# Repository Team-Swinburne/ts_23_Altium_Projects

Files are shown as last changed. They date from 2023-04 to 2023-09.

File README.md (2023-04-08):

# About

A Github repository by Team Swinburne for pcb development of the TS_22 vehicle and experimental projects. This will only contain files of the actual pcb design, more information such as design choice, circuit theory, simulation, etc can be located in the shared Pne Drive

# Getting Started

### Prerequisites
- [Altium](https://www.altium.com/solutions/academic-programs/student-licenses) (required): Used to design all of these pcb, fill in the link for a free student license.
- [Git](https://git-scm.com/) (required) : Backbone of Github.
- [Github Destop](https://desktop.github.com/) (recommended) : An UI overlay of git built specifically for Github so you don't have to deal with the terminal interface.

### Installation
Once all prerequisite are install, clone this repository to your desired folder by opening it in Github Desktop


# Usage
Follow this guide to ensure you meet the standard and is set up probably before diving into create your own pcb

### Naming
**Always** name your project strictly following the naming scheme to avoid confusion in the future. When starting a new board, create a new folder name `ts_22-"Board name"`. Then inside that folder, create a project in Altium called `YYMMDD "Board name" "Revsion number"`
#### For example:
> ts_22-Brake-Module
>
Then:
> 210705 Brake Module R0
> 
`YYMMDD` is the project's createtion date and `Revision number` starts with 0. 
#### Note: Once the pcb is made, **DO NOT** make any changes to that revision, modifying **MUST** be made by starting a new revision, e.g. R1

### Importing libraries
Altium libraries are collections of component intented for speeding up the design and manufacturing process. There are 2 libraries used in PnE: *ts_22-standard-lib* and *ts_22-connectors-lib*, located in the *~ts_22 Library*.

To import them: In Altium with your project opened, right-click on the project name -> Add Existing -> Choose file `"library name".DbLib`, do this for both libraries.



Guide on how to add components into the library will be made available in video from. Please discuss with your section leader before attempting to modify these library.

### Importing design rules
Design rules ensure all pcb meet Team Swinburne standards and more importantly, the competition rule. There are 2 sets of rules: *ts_22-rules.RUL* and *ts_22-HV-rules.RUL*. Choose the corresponding rule dependent on which board you are working on.

To import: In Altium with your project opened, choose Design -> Rules. Then in the pop-up windows, right-click on Design Rules -> Import Rules -> Select all entries -> OK -> Choose file `"rules name".RUL`.



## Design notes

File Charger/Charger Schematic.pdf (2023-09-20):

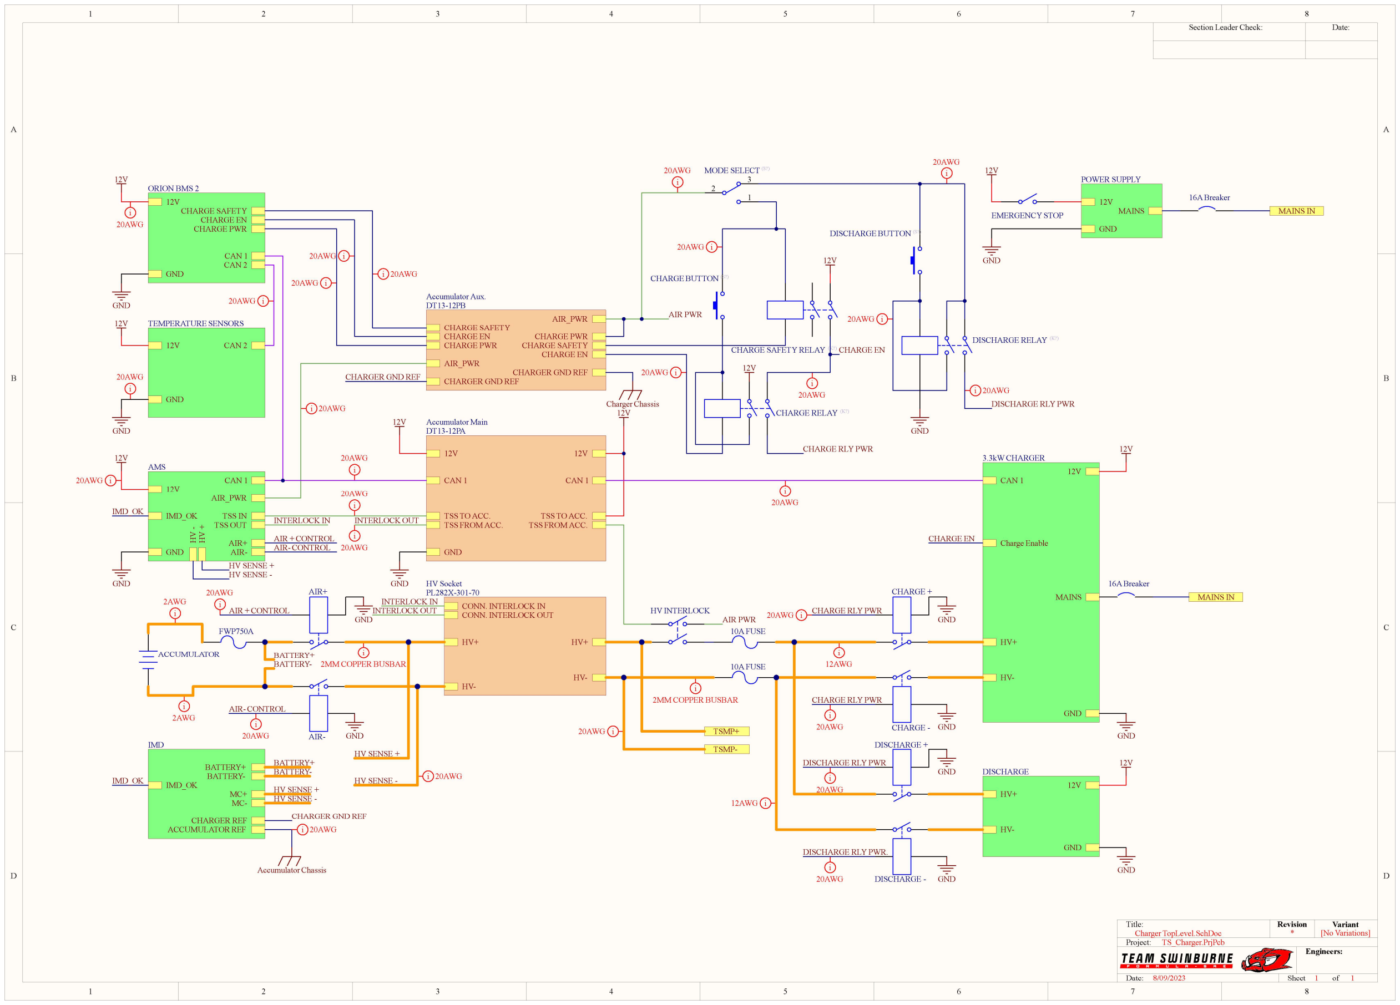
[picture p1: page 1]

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
Engineers:

Date: | Sheet | of 8/09/2023 | 1 | 1

Project:

Title: | Revision | Variant
Section Leader Check: | Date:

Charger TopLevel.SchDoc
TS_Charger.PrjPcb

* [No Variations]

12V

GND

CHARGE PWR

CHARGE SAFETY
CHARGE EN

CAN 1
CAN 2

ORION BMS 2

12V

GND

CAN 2

GND

12V

12V TEMPERATURE SENSORS

GND

CAN 1

GND

12V HV ⁻ HV ⁺

TSS IN
TSS OUT

AIR_PWR

AIR+
AIR-

IMD_OK

AMS

GND

12V

CHARGE SAFETY
CHARGE EN
CHARGE PWR

AIR_PWR

AIR_PWR

CHARGE SAFETY
CHARGE EN

CHARGE PWR

CHARGER GND REF

CHARGER GND REF

Accumulator Aux.
DT13-12PB

12V

GND

CAN 1

TSS TO ACC.
TSS FROM ACC.

TSS TO ACC.
TSS FROM ACC.

12V

CAN 1

Accumulator Main
DT13-12PA

12V

GND

HV+

HV-

HV+

HV-

CONN. INTERLOCK IN
CONN. INTERLOCK OUT

HV Socket
PL282X-301-70

12V

GND

MAINS

POWER SUPPLY

12V

GND

DISCHARGE RELAY (K?)

16A Breaker
MAINS IN

DISCHARGE BUTTON ⁽S?)

2

3

1

MODE SELECT ⁽S?)

12V

CHARGE SAFETY RELAY (K?)

12V

GND

DISCHARGE RLY PWR

CHARGE EN

CHARGE RELAY (K?)

CHARGE BUTTON ⁽S?)

12V

CHARGE RLY PWR

HV INTERLOCK

AIR PWR

AIR PWR

CAN 1

GND

12V

HV+

HV-

MAINS

Charge Enable

3.3kW CHARGER

CHARGE -

CHARGE +

GND

GND

CHARGE RLY PWR

CHARGE RLY PWR

GND

12V

16A Breaker
MAINS IN

10A FUSE

10A FUSE

DISCHARGE -

DISCHARGE +

GND

GND

DISCHARGE RLY PWR

DISCHARGE RLY PWR.

CHARGE EN

HV+

GND

12V

HV-

DISCHARGE

GND

12V

TSMP+

TSMP-

AIR-

AIR+

GND

GND

AIR + CONTROL

AIR- CONTROL

AIR + CONTROL
AIR- CONTROL

ACCUMULATOR

FWP750A

HV SENSE +
HV SENSE -

HV SENSE +

HV SENSE - | i 20AWG

i

20AWG

i

20AWG

i
20AWG

20AWG i

i

20AWG

20AWG i

i
20AWG

i 20AWG
20AWG i

20AWG i

i 20AWG

i

20AWG

i
20AWG

20AWG i

i
20AWG

i
20AWG

i
20AWG

i
20AWG

20AWG i

20AWG i

i

20AWG | i 20AWG

i 20AWG

20AWG i

i
20AWG

i
12AWG

12AWG i

i
2MM COPPER BUSBAR

20AWG i

i

2AWG

i
2AWG

i
2MM COPPER BUSBAR

BATTERY+
BATTERY-IMD_OK

CHARGER REF
ACCUMULATOR REF

MC+
MC-

IMD

EMERGENCY STOP

INTERLOCK IN

INTERLOCK IN
INTERLOCK OUT

INTERLOCK OUT

HV SENSE +
HV SENSE -

BATTERY+
BATTERY-

BATTERY+
BATTERY-

Accumulator Chassis

IMD_OK

IMD_OK

Charger Chassis

CHARGER GND REF

CHARGER GND REF
i 20AWG

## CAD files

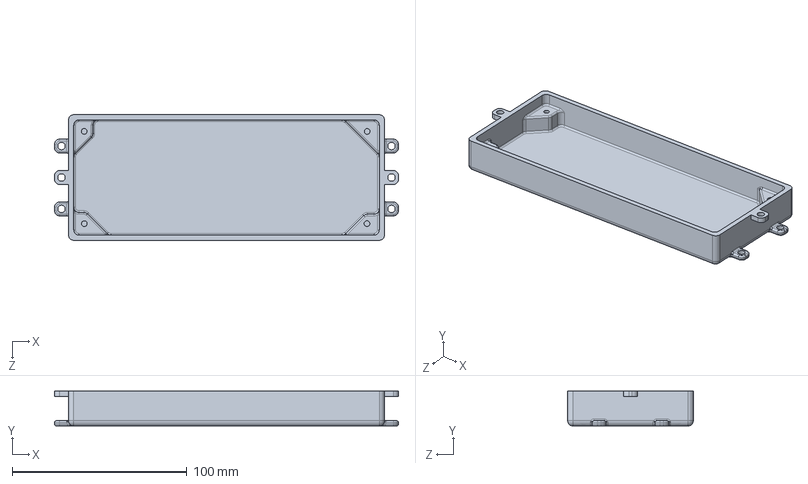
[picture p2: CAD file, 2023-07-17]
TS_23_Temp Expansion Module/Temp Module Assembly CAD/Temp_Module_Enclosure_Base.SLDPRT
197.0 x 20.0 x 72.0 mm

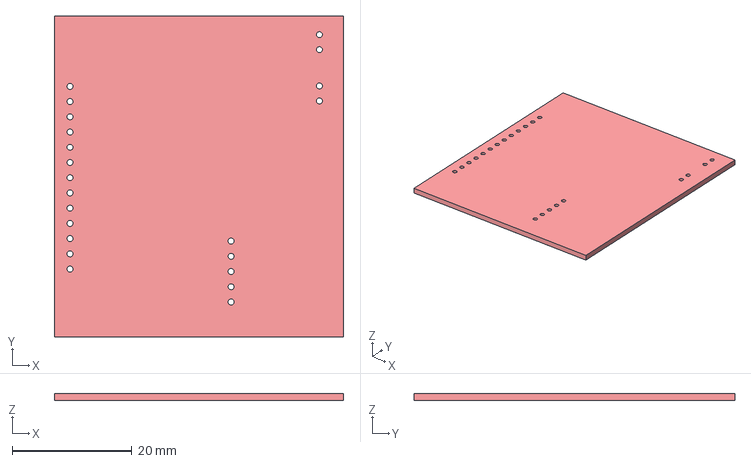
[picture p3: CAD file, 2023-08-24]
ts_23_BMS_SLAVE/LVBMS_A_Sample_R2/LVBMS_A_Sample_R2.step
48.2 x 53.5 x 1.20 mm

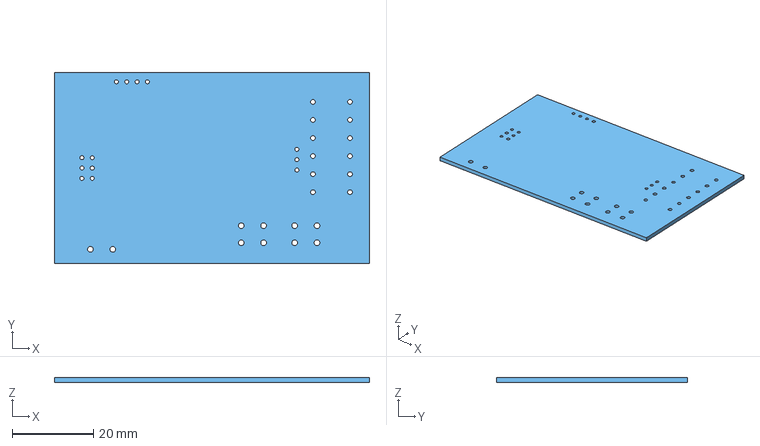
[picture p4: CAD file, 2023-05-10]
ts_23_LV_BMS_MASTER/LV_MASTER_A_SAMPLE/LV_MASTER_A_SAMPLE.step
77.5 x 46.9 x 1.20 mm

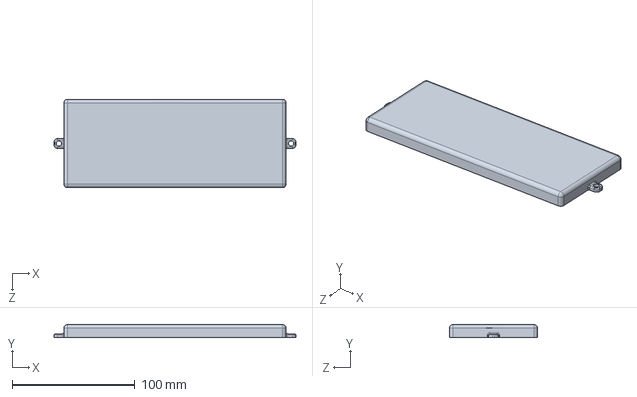
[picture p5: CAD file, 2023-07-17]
TS_23_Temp Expansion Module/Temp Module Assembly CAD/Temp_Module_Enclosure_Lid.SLDPRT
197.0 x 10.5 x 72.0 mm

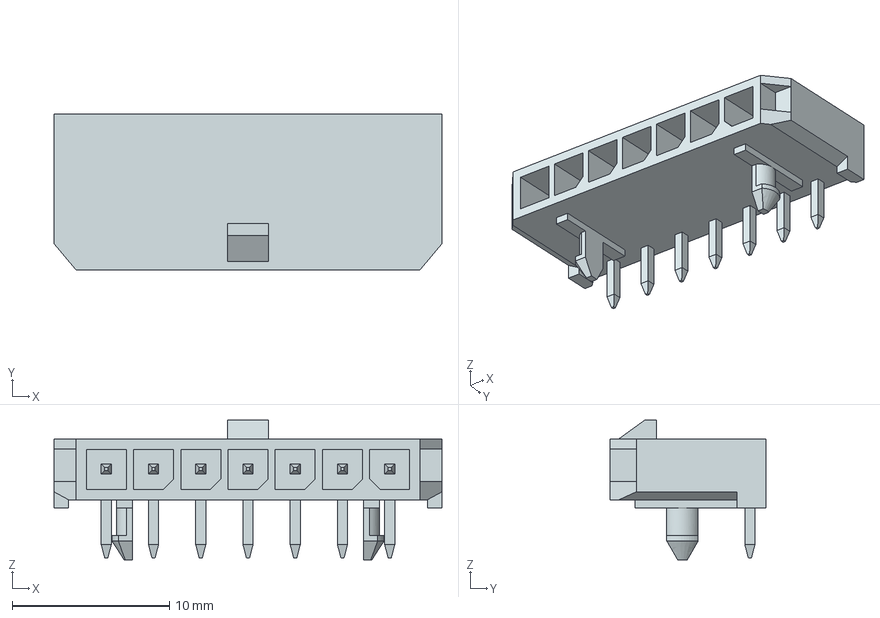
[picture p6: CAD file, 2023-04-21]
TS_23 Dashboard Breakout Board/436500700.stp
24.6 x 9.90 x 8.87 mm

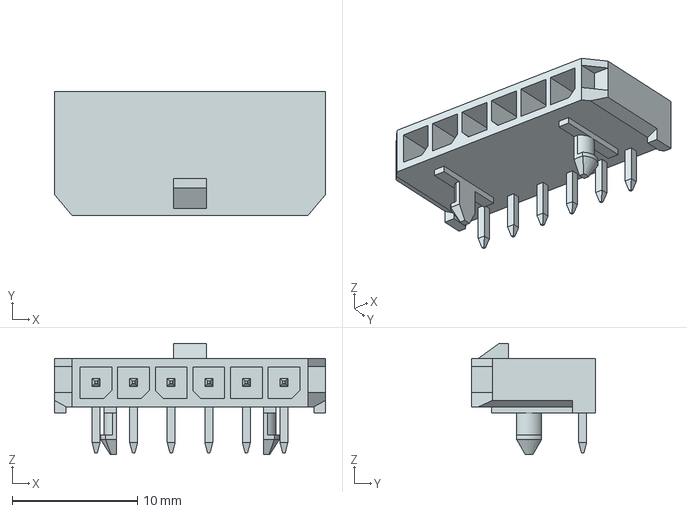
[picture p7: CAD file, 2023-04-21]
TS_23 Dashboard Breakout Board/436500600.stp
21.6 x 9.90 x 8.87 mm

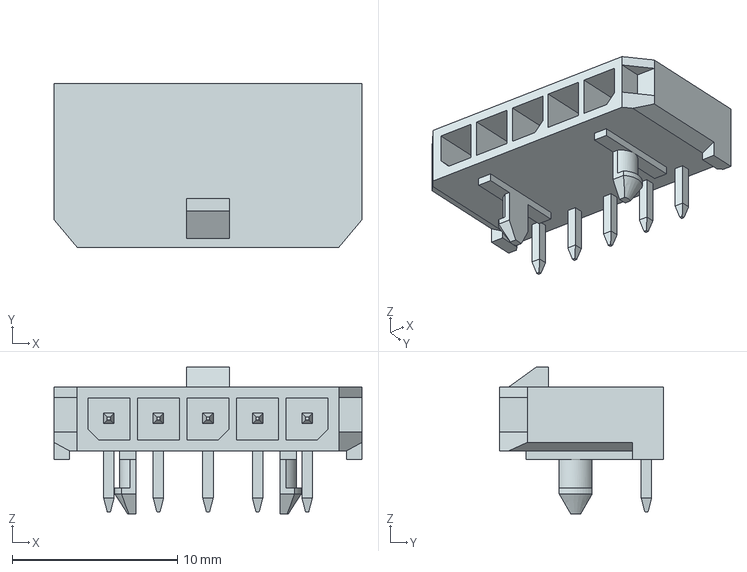
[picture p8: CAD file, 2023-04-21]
TS_23 Dashboard Breakout Board/436500500.stp
18.6 x 9.90 x 8.87 mm

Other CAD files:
ts_23_BMS_SLAVE/LVBMS_A_Sample_R2/LVBMS_A_Sample_R2 PCB.step.SLDPRT
ts_23_LV_BMS_MASTER/LV_MASTER_A_SAMPLE/LV_MASTER_A_SAMPLE PCB.step.SLDPRT

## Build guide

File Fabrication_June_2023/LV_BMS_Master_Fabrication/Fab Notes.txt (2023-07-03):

------------------------------------
-----LV BMS MASTER FAB NOTES-------
-----------------------------------

Qty: 5
Dimensions: 90.5mm X 49.9mm
Layers: 4
Signal Layers: 1, 2
	a) Weight: 1oz
Solder Mask: Blue
Silkscreen: White
Surface Finish: ENIG
Finished Copper: 2oz Cu
Total Thickness: 1.6mm

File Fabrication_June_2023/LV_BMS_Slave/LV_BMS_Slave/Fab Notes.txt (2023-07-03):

------------------------------------
-----LV BMS Slave Fab Notes-------
-----------------------------------

Qty: 10
Dimensions: 48.2mm X 53.5mm
Layers: 2
Signal Layers: 1, 2
	a) Weight: 1oz
Solder Mask: Red
Silkscreen: White
Surface Finish: ENIG
Finished Copper: 2oz Cu
Total Thickness: 1.6mm

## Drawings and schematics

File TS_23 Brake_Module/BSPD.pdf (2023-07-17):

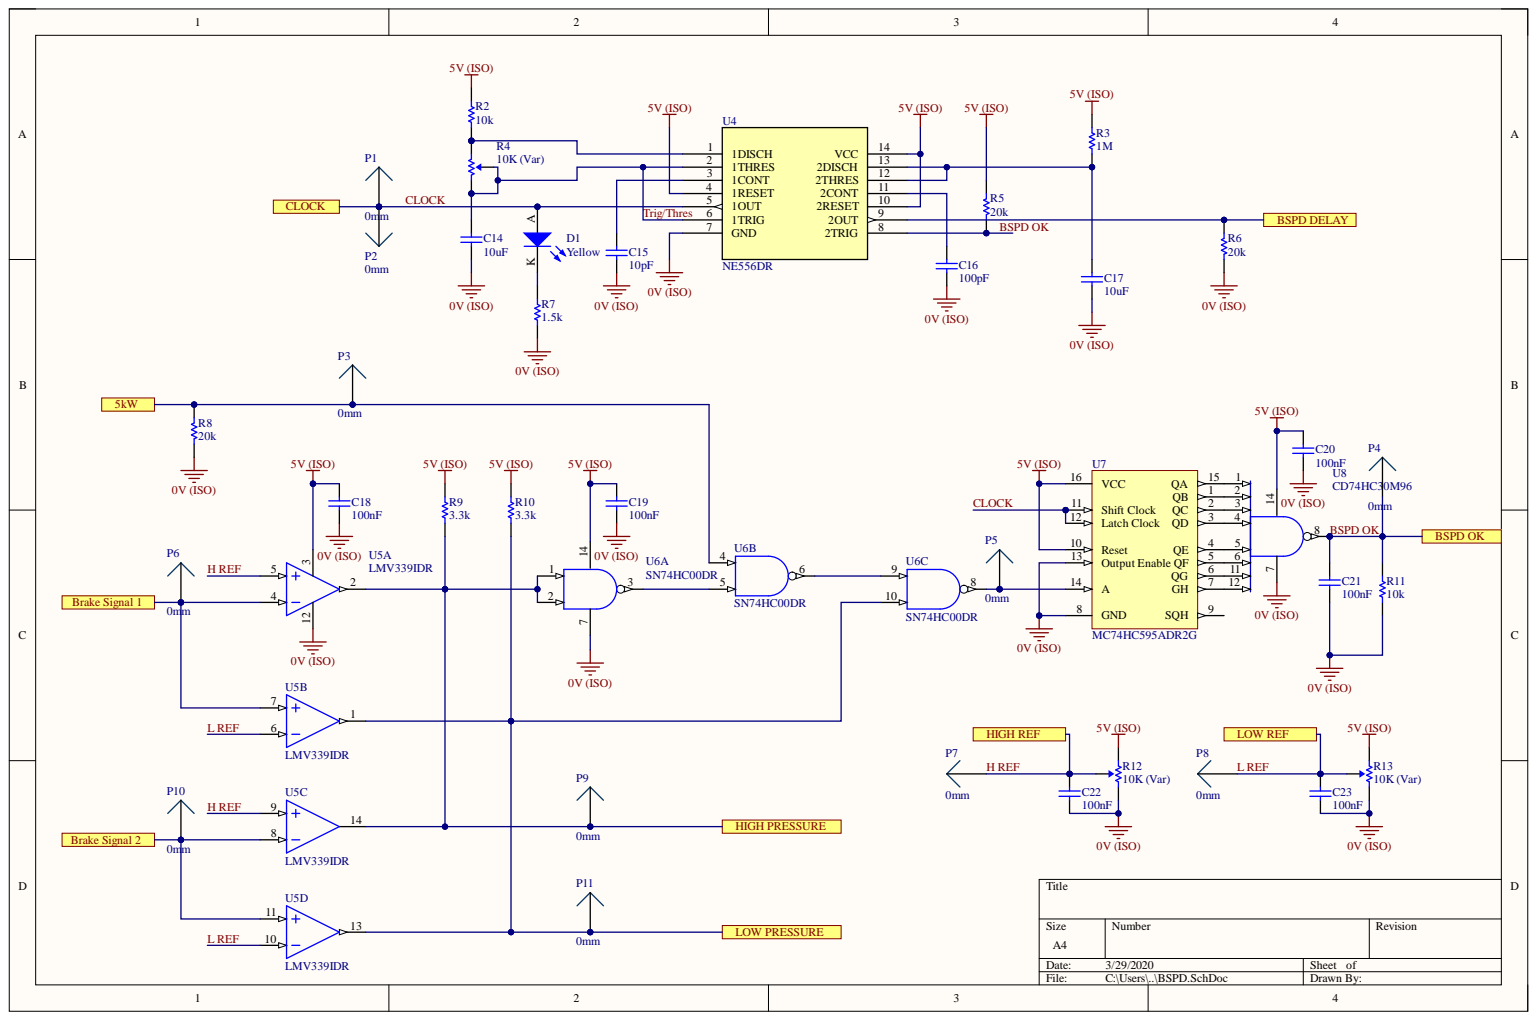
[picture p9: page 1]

1THRES 2

1RESET 4

Trig/Thres | 1TRIG 6

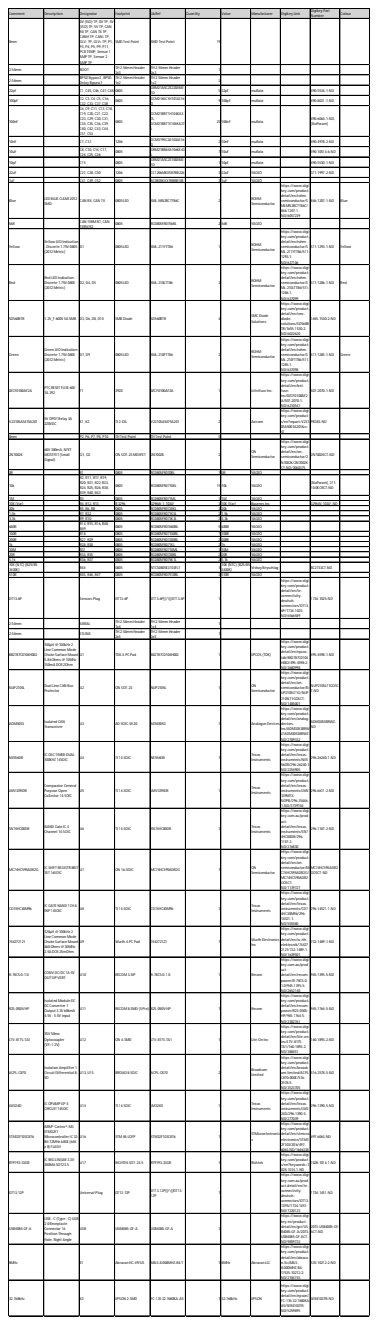
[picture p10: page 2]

Comment | Description | Designator | Footprint | LibRef | Quantity | Value | Manufacturer | Digikey Link | Digikey Part Number | Colour

0mm | | 0V (ISO) TP, 0V TP, 5V (ISO) TP, 5V TP, CAN RX TP, CAN TX TP, CANH TP, CANL TP, GLV- TP, GLV+ TP, P1, P3, P4, P5, P9, P11, PCB TEMP, Sensor 1 AMP TP, Sensor 2 AMP TP | SMD Test Point | SMD Test Point | 19

2.54mm | | BOOT | TH 2.54mm Header 2x3 | TH 2.54mm Header 2x3 | | 1

2.54mm | | BPSD Bypass1, BPSD Delay Bypass1 | TH 2.54mm Header 1x2 | TH 2.54mm Header 1x2 | | 2

22pF | | C1, C45, C46, C47, C48 | 0805 | GRM21A5C2E220JW0 1D | | 5 22pF | muRata | | 490-5534-1-ND

100pF | | C2, C3, C4, C5, C16, C32, C33, C37, C38 | 0805 | GCM2165C1H101JA16 D | | 9 100pF | muRata | | 490-8031-1-ND

100nF | | C6, C9, C11, C13, C18, C19, C20, C21, C22, C23, C29, C30, C31, C34, C35, C36, C39, C40, C42, C43, C44, C51, C53 | 0805 | GCM21BR71H104KA3 7L, GCM21BR71E104KA37 L | 23 100nF | | muRata | | 490-6064-1-ND, [NoParam]

10nF | | C7, C12 | 1206 | GCM3195C2A103JA16 D | | 2 10nF | muRata | | 490-4978-2-ND

10uF | | C8, C10, C14, C17, C24, C25, C26 | 0805 | GRM21BR6YA106KE43 L | | 7 10uF | muRata | | 490-10514-6-ND

10pF | | C15 | 0805 | GRM21A5C2E100JW0 1D | | 1 10pF | muRata | | 490-5530-1-ND

22uF | | C27, C28, C50 | 1206 | CC1206MKX5R7BB226 | | 3 22uF | YAGEO | | 311-1997-2-ND

1uF Blue | LED BLUE CLEAR 2012 SMD | C41, C49, C52 CAN RX, CAN TX | 0805 0805 LED | AC0805KKX7R8BB105 SML-MN2BCTT86C | | 3 1uF 2 | YAGEO ROHM Semiconductor | https://www.digikey.com/product-detail/en/rohm-semiconductor/SMLMN2BCTT86C/846-1207-1-ND/6057239 | 846-1207-1-ND | Blue

56R | | CAN TERM R1, CAN TERM R2 | 0805 | RC0805FR0756RL | 2 56R | YAGEO

Yellow | Yellow LED Indication - Discrete 1.75V 0805 (2012 Metric) | D1 | 0805 LED | SML-211YTT86 | 1 | ROHM Semiconductor | https://www.digikey.com/product-detail/en/rohm-semiconductor/SML-211YTT86/511-1293-1-ND/637106 | 511-1293-1-ND | Yellow

Red | Red LED Indication -Discrete 1.75V 0805 (2012 Metric) | D2, D4, D5 | 0805 LED | SML-210LTT86 | 3 | ROHM Semiconductor | https://www.digikey.com/product-detail/en/rohm-semiconductor/SML-210LTT86/511-1286-1-ND/637099 | 511-1286-1-ND | Red

SD560BTR | 1.2V_F 600V 5A SMB | D3, D6, D8, D10 | SMB Diode | SD560BTR | 4 | SMC Diode Solutions | https://www.digikey.com/product-detail/en/smc-diode-solutions/SD560BTR/1655-1530-2-ND/6022620 | 1655-1530-2-ND

Green | Green LED Indication -Discrete 1.75V 0805 (2012 Metric) | D7, D9 | 0805 LED | SML-210FTT86 | 2 | ROHM Semiconductor | https://www.digikey.com/product-detail/en/rohm-semiconductor/SML-210FTT86/511-1285-1-ND/637098 | 511-1285-1-ND | Green

0ZCF0100AF2A | PTC RESET FUSE 60V 1A 292 | F1 | 2920 | 0ZCF0100AF2A | 1 | Littelfuse Inc. | https://www.digikey.com/product-detail/en/bel-fuse-inc/0ZCF0100AF2A/507-2070-1-ND/6210547 | 507-2070-1-ND

V23105A5475A201 | 5V DPDT Relay 3A 220VDC | K1, K2 | TI 2-DIL | V23105A5475A201 | 2 | Axicom | https://www.digikey.com/products/en?mpart=V23105A5001A201&v=41 | PB383-ND

0mm 2N7002K | 60V 380mA, NFET MOSTFET (Small Signal) | P2, P6, P7, P8, P10 Q1, Q2 | TH Test Point ON SOT-23 MOSFET | TH Test Point 2N7002K | 5 2 | ON Semiconductor | https://www.digikey.com/product-detail/en/on-semiconductor/2N7002K/2N7002KCT-ND/2060375 | 2N7002KCT-ND

0R 10k | R1 R2, R11, R17, R19, R20, R21, R22, R23, R24, R25, R26, R38, R39, R40, R43 | 0805 | RC0805FR070RL RC0805FR0710KL | 15 10k | 1 0R | YAGEO | [NoParam], 311-10.0KCRCT-ND

5.1k 10K (NTC) (B25/85 3430K) | R36, R37 R44 | 0805 | RC0805FR075K1L NTCS0805E3103FLT | 2 5.1k 1 10K (NTC) (B25/85 3430K) | YAGEO Vishay Beyschlag | BC2733CT-ND

510R DT13-6P | R45, R46, R47 Sensors Plug | 0805 DT13-6P | RC0805FR07510RL DT13-6P[[/\]]DT13-6P | 3 510R 1 | YAGEO | https://www.digikey.com/product-detail/en/te-connectivity-deutsch-connectors/DT13-6P/1734-1025-ND/6566589 | 1734-1025-ND

2.54mm | | SERIAL | TH 2.54mm Header 1x4 | TH 2.54mm Header 1x4 | 1

2.54mm | | STLINK | TH 2.54mm Header 2x5 | TH 2.54mm Header 2x5 | 1

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

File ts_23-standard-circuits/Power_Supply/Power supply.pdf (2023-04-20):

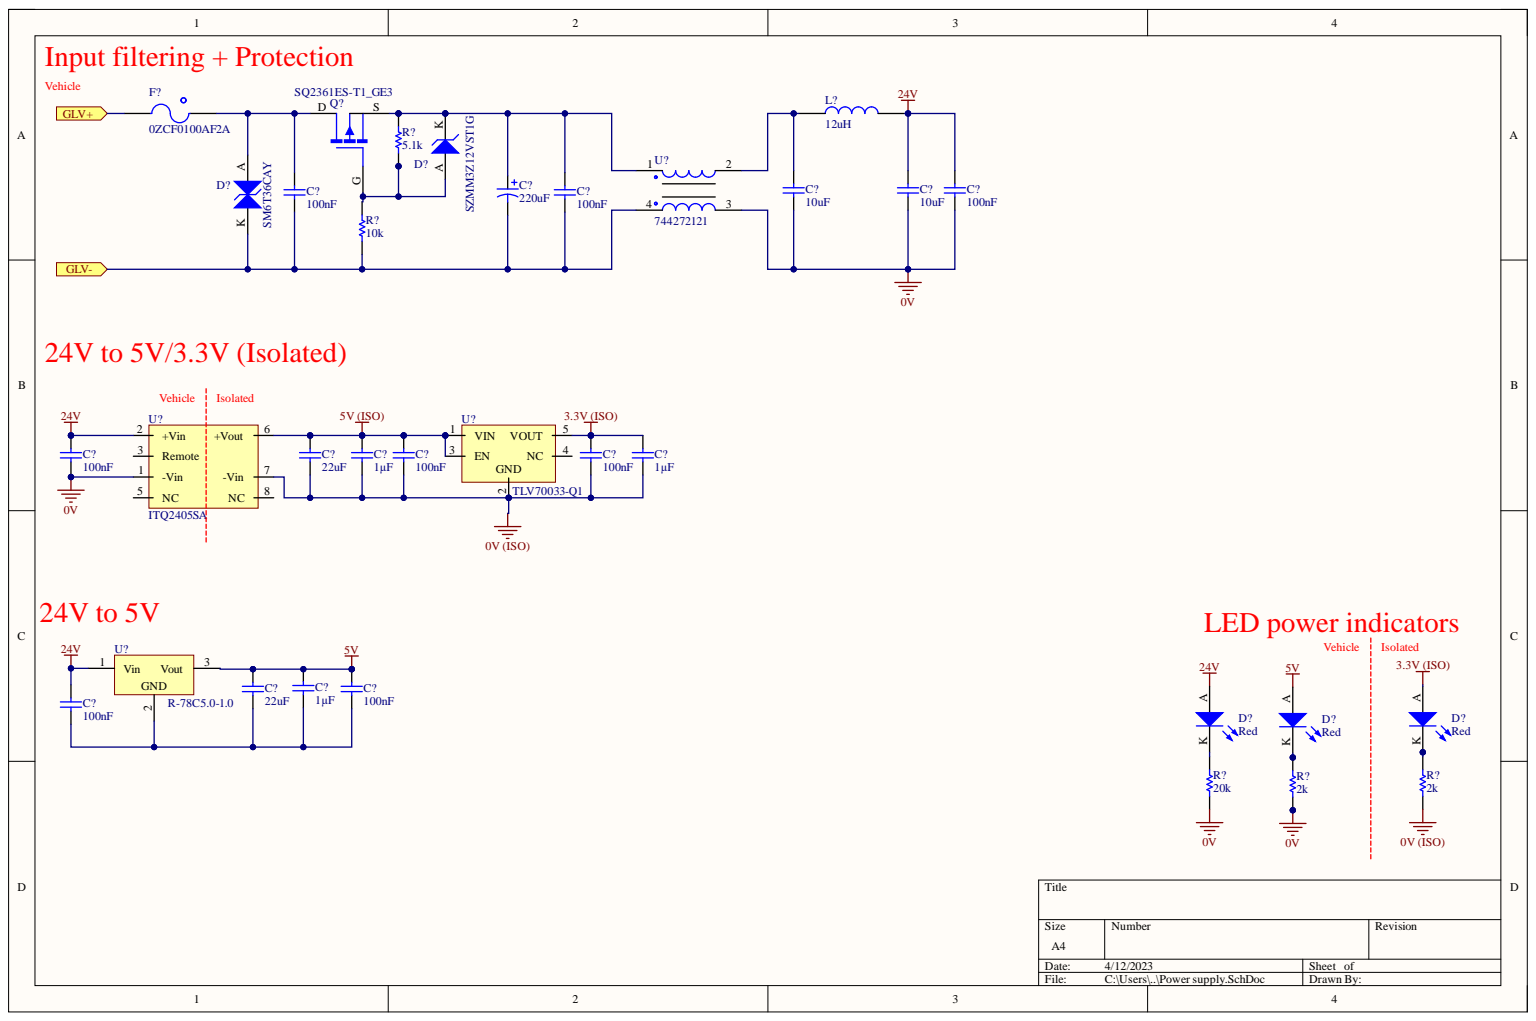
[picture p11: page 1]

Comment | Description | Designator | Footprint | LibRef | Quantity
220uF | | C6, C? | Vishay Radial 1213 | MAL214699106E3 | 2
10uF | | C7, C8, C? | 0805 | GRM21BR6YA106KE4 3L | 4
100nF | | C9, C10, C11, C12, C15, C16, C? | 0805 | GCM21BR71H104KA3 7L | 12
22uF | | C13, C? | 0805 | GRM21BR61A226ME5 1L | 2
1µF | | C14, C17, C? | 0805 | GCM21BR71H105KA0 3L | 4
SZMM3Z12VST1G | | D2, D? | ON SOD323 | SZMM3Z12VST1G | 2
SM6T36CAY | | D3, D? | ST SMB DIODE | SM6T36CAY | 2
Red | [NoValue], Red LED Indication - Discrete 1.75V 0805 (2012 Metric) | D4, D5, D? | 0805 LED | Red, SML-210LTT86 | 4
0ZCF0100AF2A | PTC RESET FUSE 60V 1A 292 | F2, F? | 2920 | 0ZCF0100AF2A | 2
12uH | | L1, L? | 1812 | RLS-126 | 2
SQ2361ES-T1_GE3 | MOSFET P-CH 60V 2.8A SSOT23 | Q1, Q? | VSHY SOT-23-3 | SQ2361ES-T1_GE3 | 2
5.1k | | R1, R? | 0805 | RC0805FR075K1L | 2
10k | | R2, R? | 0805 | RC0805FR0710KL | 2
20k | | R3, R? | 0805 | RC0805FR0720KL | 2
2k | | R4, R? | 0805 | RC0805FR072KL | 2
744272121 | | U3, U? | Wurth 4-PC Pad | 744272121 | 2
ITQ2405SA | DC DC CONVERTER 5V 6W | U4, U? | 8-SIP | ITQ2405SA | 2
TLV70033-Q1 | IC REG LINEAR 3.3V 200MA SOT23-5 | U5, U? | TI SOT-23-5 | TLV70033-Q1 | 2

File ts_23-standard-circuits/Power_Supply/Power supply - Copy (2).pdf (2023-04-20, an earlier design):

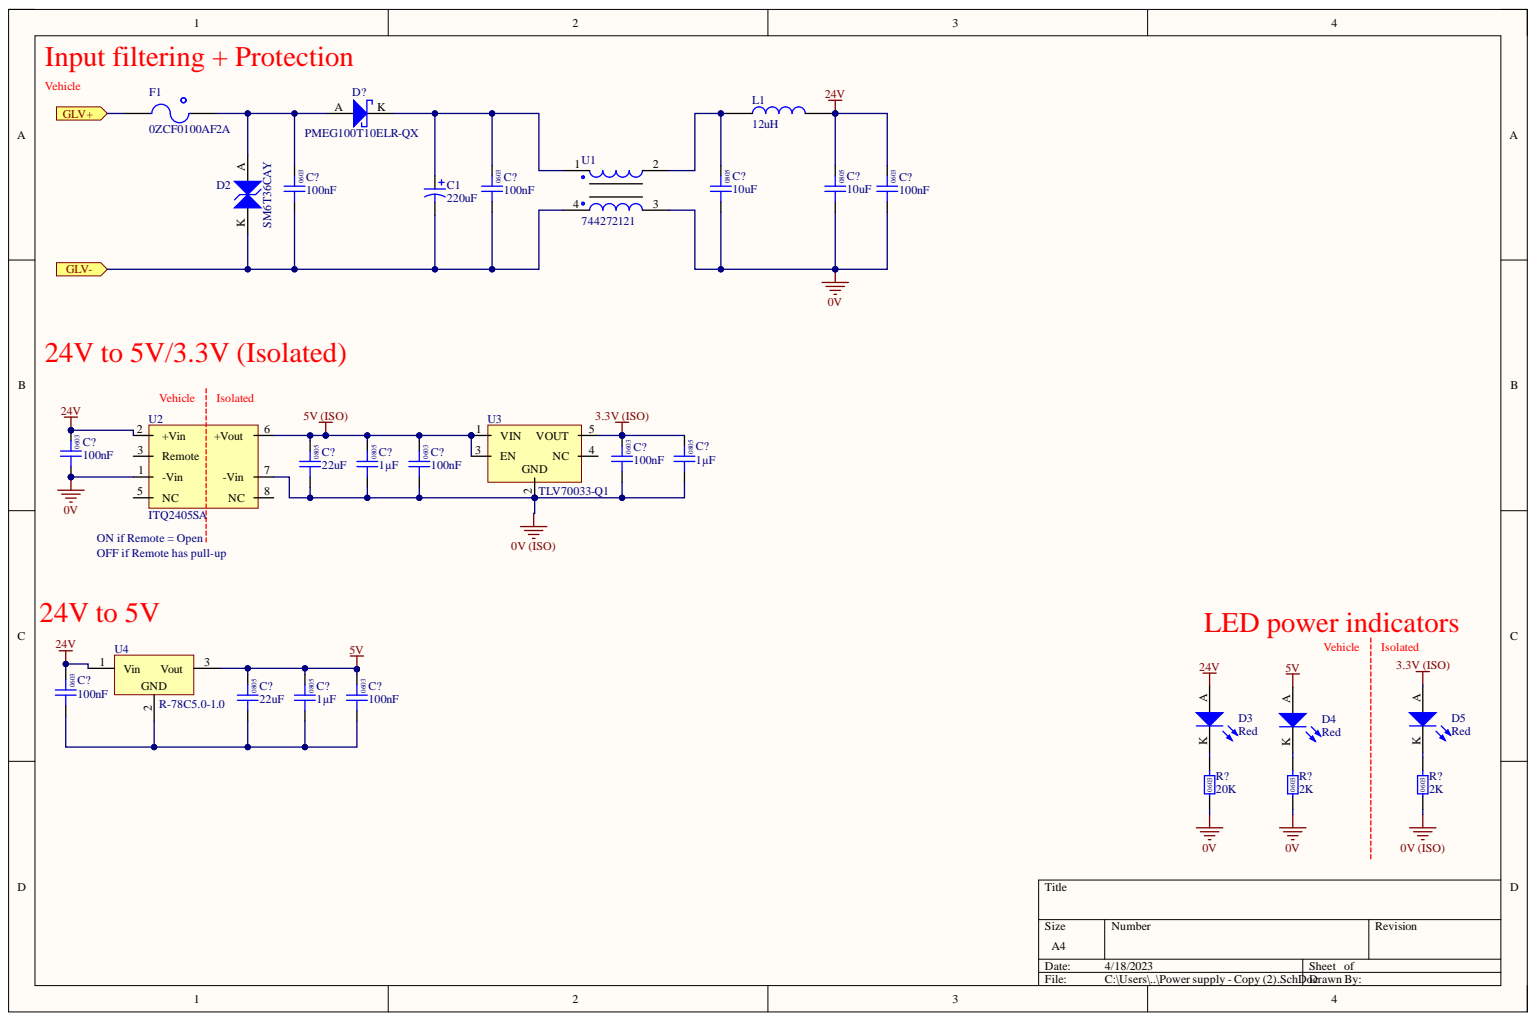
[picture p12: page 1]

Remote 3 -Vin 1 | EN 3

TLV70033-Q1

ON if Remote = Open
OFF if Remote has pull-up

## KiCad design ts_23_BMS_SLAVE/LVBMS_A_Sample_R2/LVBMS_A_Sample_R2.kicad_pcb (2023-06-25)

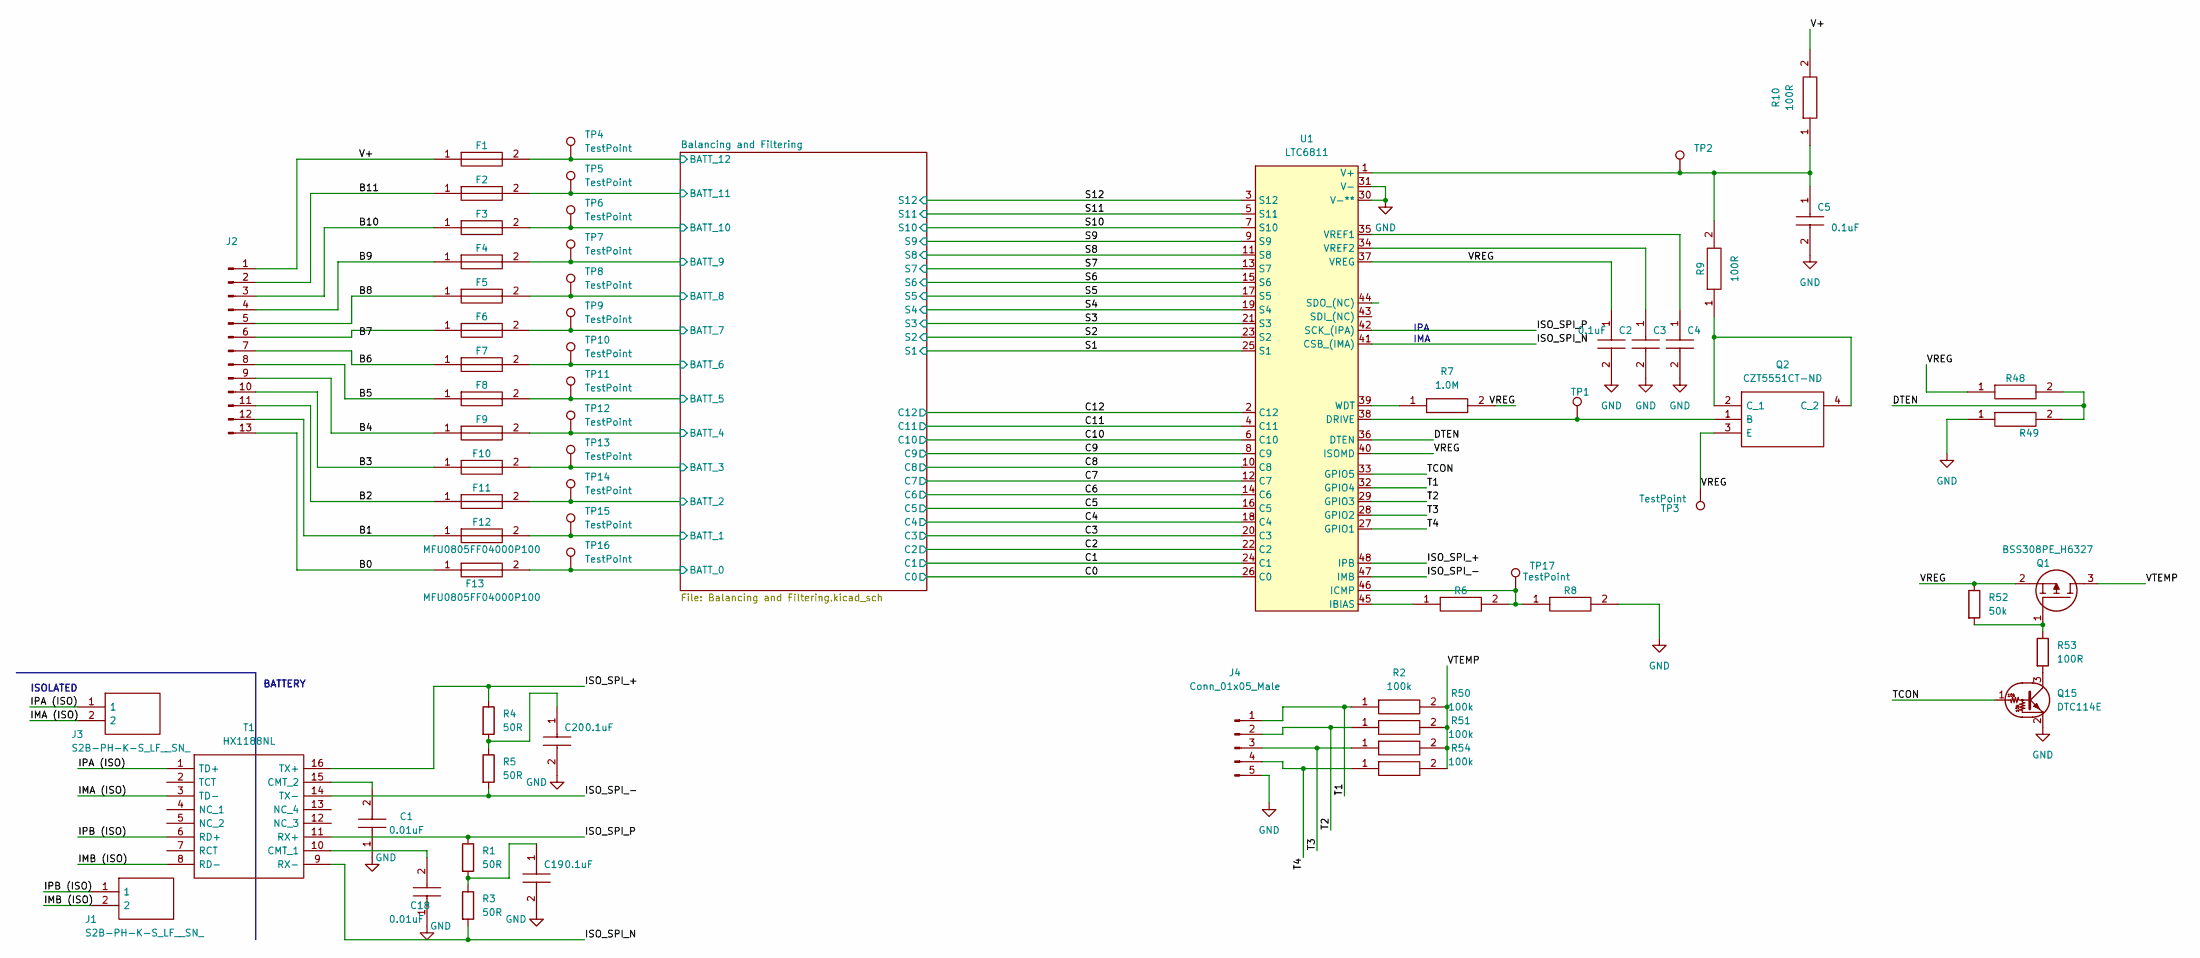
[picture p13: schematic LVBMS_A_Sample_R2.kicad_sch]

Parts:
C1, C18: 0.01uF; C_0603_1608Metric_Pad1.08x0.95mm_HandSolder; Manufacturer_Part_Number CC0805JRX7R9BB103
C2, C3, C4, C5, C19, C20: 0.1uF; C_0603_1608Metric_Pad1.08x0.95mm_HandSolder; Manufacturer_Part_Number CC0805JRX7R8BB104; Mouser Part Number 603-CC805JRX7R8BB104
F1, F2, F3, F4, F5, F6, F7, F8, F9, F10, F11, F12, F13: MFU0805FF04000P100; Fuse_0603_1608Metric_Pad1.05x0.95mm_HandSolder; Manufacturer_Part_Number MFU0805FF04000P100; Mouser Part Number 594-MFU0805FF04000P1
J1, J3: S2B-PH-K-S_LF__SN_; JST_EH_B2B-EH-A_1x02_P2.50mm_Vertical; Manufacturer_Part_Number S2B-PH-K-S(LF)(SN)
J2: Conn_01x13_Male; PinSocket_1x13_P2.54mm_Vertical
J4: Conn_01x05_Male; PinSocket_1x05_P2.54mm_Vertical
Q1: BSS308PE_H6327; SOT95P260X110-3N; Manufacturer_Part_Number BSS308PE H6327; Mouser Part Number 726-BSS308PEH6327
Q2: CZT5551CT-ND; SOT230P700X180-4N; Manufacturer_Part_Number CZT5551CT-ND
Q15: DTC114E; SOT-23
R1, R3, R4, R5: 50R; R_0603_1608Metric_Pad0.98x0.95mm_HandSolder
R2, R50, R51, R54: 100k; R_0603_1608Metric_Pad0.98x0.95mm_HandSolder; Manufacturer_Part_Number ERJP06F1000V
R6: BIAS RESISTOR (VALUE CHANGES); R_0603_1608Metric_Pad0.98x0.95mm_HandSolder; Manufacturer_Part_Number ERJP06F1000V
R7: 1.0M; R_0603_1608Metric_Pad0.98x0.95mm_HandSolder; Manufacturer_Part_Number ERJ-P06J105V; Mouser Part Number 667-ERJ-P06J105V
R8: BIAS RESISTOR (VALUE CAN CHANGE); R_0603_1608Metric_Pad0.98x0.95mm_HandSolder; Manufacturer_Part_Number ERJP06F1000V
R9, R10, R48, R49: 100R; R_0603_1608Metric_Pad0.98x0.95mm_HandSolder; Manufacturer_Part_Number ERJP06F1000V
R52: 50k; R_0603_1608Metric_Pad0.98x0.95mm_HandSolder
R53: 100R; R_0603_1608Metric_Pad0.98x0.95mm_HandSolder
T1: HX1188NL; SOIC127P940X597-16N; Manufacturer_Part_Number HX1188NL; Mouser Part Number 673-HX1188NL
TP1, TP2, TP3, TP4, TP5, TP6, TP7, TP8, TP9, TP10, TP11, TP12, TP13, TP14, TP15, TP16, TP17: TestPoint; TestPoint_Pad_D1.0mm
U1: LTC6811

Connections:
/B0: F13.1, J2.13
/B1: F12.1, J2.12
/B2: F11.1, J2.11
/B3: F10.1, J2.10
/B4: F9.1, J2.9
/B5: F8.1, J2.8
/B6: F7.1, J2.7
/B8: F5.1, J2.5
/B9: F4.1, J2.4
/B10: F3.1, J2.3
/B11: F2.1, J2.2
/Balancing and Filtering/BATT_0: F13.2, TP16.1; also elsewhere on the board
/Balancing and Filtering/BATT_1: F12.2, TP15.1; also elsewhere on the board
/Balancing and Filtering/BATT_2: F11.2, TP14.1; also elsewhere on the board
/Balancing and Filtering/BATT_3: F10.2, TP13.1; also elsewhere on the board
/Balancing and Filtering/BATT_4: F9.2, TP12.1; also elsewhere on the board
/Balancing and Filtering/BATT_5: F8.2, TP11.1; also elsewhere on the board
/Balancing and Filtering/BATT_6: F7.2, TP10.1; also elsewhere on the board
/Balancing and Filtering/BATT_7: F6.2, TP9.1; also elsewhere on the board
/Balancing and Filtering/BATT_8: F5.2, TP8.1; also elsewhere on the board
/Balancing and Filtering/BATT_9: F4.2, TP7.1; also elsewhere on the board
/Balancing and Filtering/BATT_10: F3.2, TP6.1; also elsewhere on the board
/Balancing and Filtering/BATT_11: F2.2, TP5.1; also elsewhere on the board
/Balancing and Filtering/BATT_12: F1.2, TP4.1; also elsewhere on the board
/C1: U1.24 (C1); also elsewhere on the board
/C2: U1.22 (C2); also elsewhere on the board
/C3: U1.20 (C3); also elsewhere on the board
/C4: U1.18 (C4); also elsewhere on the board
/C5: U1.16 (C5); also elsewhere on the board
/C6: U1.14 (C6); also elsewhere on the board
/C7: U1.12 (C7); also elsewhere on the board
/C8: U1.10 (C8); also elsewhere on the board
/C9: U1.8 (C9); also elsewhere on the board
/C10: U1.6 (C10); also elsewhere on the board
/C11: U1.4 (C11); also elsewhere on the board
/C12: U1.2 (C12); also elsewhere on the board
/DTEN: R48.2, R49.2, U1.36 (DTEN)
/IMA (ISO): J3.2, T1.3 (TD-)
/IMB (ISO): J1.2, T1.8 (RD-)
/IPA (ISO): J3.1, T1.1 (TD+)
/IPB (ISO): J1.1, T1.6 (RD+)
/ISO_SPI_+: R4.1, T1.16 (TX+), U1.48 (IPB)
/ISO_SPI_-: R5.2, T1.14 (TX-), U1.47 (IMB)
/ISO_SPI_N: R3.2, T1.9 (RX-), U1.41 (CSB_(IMA))
/ISO_SPI_P: R1.1, T1.11 (RX+), U1.42 (SCK_(IPA))
/S1: U1.25 (S1); also elsewhere on the board
/S2: U1.23 (S2); also elsewhere on the board
/S3: U1.21 (S3); also elsewhere on the board
/S4: U1.19 (S4); also elsewhere on the board
/S5: U1.17 (S5); also elsewhere on the board
/S6: U1.15 (S6); also elsewhere on the board
/S7: U1.13 (S7); also elsewhere on the board
/S8: U1.11 (S8); also elsewhere on the board
/S9: U1.9 (S9); also elsewhere on the board
/S10: U1.7 (S10); also elsewhere on the board
/S11: U1.5 (S11); also elsewhere on the board
/S12: U1.3 (S12); also elsewhere on the board
/T1: J4.1, R2.1, U1.32 (GPIO4)
/T2: J4.2, R50.1, U1.29 (GPIO3)
/T3: J4.3, R51.1, U1.28 (GPIO2)
/T4: J4.4, R54.1, U1.27 (GPIO1)
/TCON: Q15.1 (B), U1.33 (GPIO5)
/V+: F1.1, J2.1, R10.2
/VREG: C2.1, Q1.2, Q2.3 (E), R7.2, R48.1, R52.1, TP3.1, U1.37 (VREG), U1.40 (ISOMD)
/VTEMP: Q1.3, R2.2, R50.2, R51.2, R54.2
GND: C1.1, C2.2, C3.2, C4.2, C5.2, C18.1, C19.2, C20.2, J4.5, Q15.2 (E), R8.2, R49.1, U1.26 (C0), U1.30 (V-**), U1.31 (V-); also elsewhere on the board
unnamed: C1.2, T1.15 (CMT_2)
unnamed: C3.1, U1.34 (VREF2)
unnamed: C4.1, U1.35 (VREF1)
unnamed: C5.1, R9.2, R10.1, TP2.1, U1.1 (V+)
unnamed: C18.2, T1.10 (CMT_1)
unnamed: C19.1, R1.2, R3.1
unnamed: C20.1, R4.2, R5.1
unnamed: F6.1, J2.6
unnamed: Q1.1, R52.2, R53.1
unnamed: Q2.1 (B), TP1.1, U1.38 (DRIVE)
unnamed: Q2.2 (C_1), Q2.4 (C_2), R9.1
unnamed: Q15.3 (C), R53.2
unnamed: R6.1, U1.45 (IBIAS)
unnamed: R6.2, R8.1, TP17.1, U1.46 (ICMP)
unnamed: R7.1, U1.39 (WDT)

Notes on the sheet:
IPA IMA
BATTERY
ISOLATED

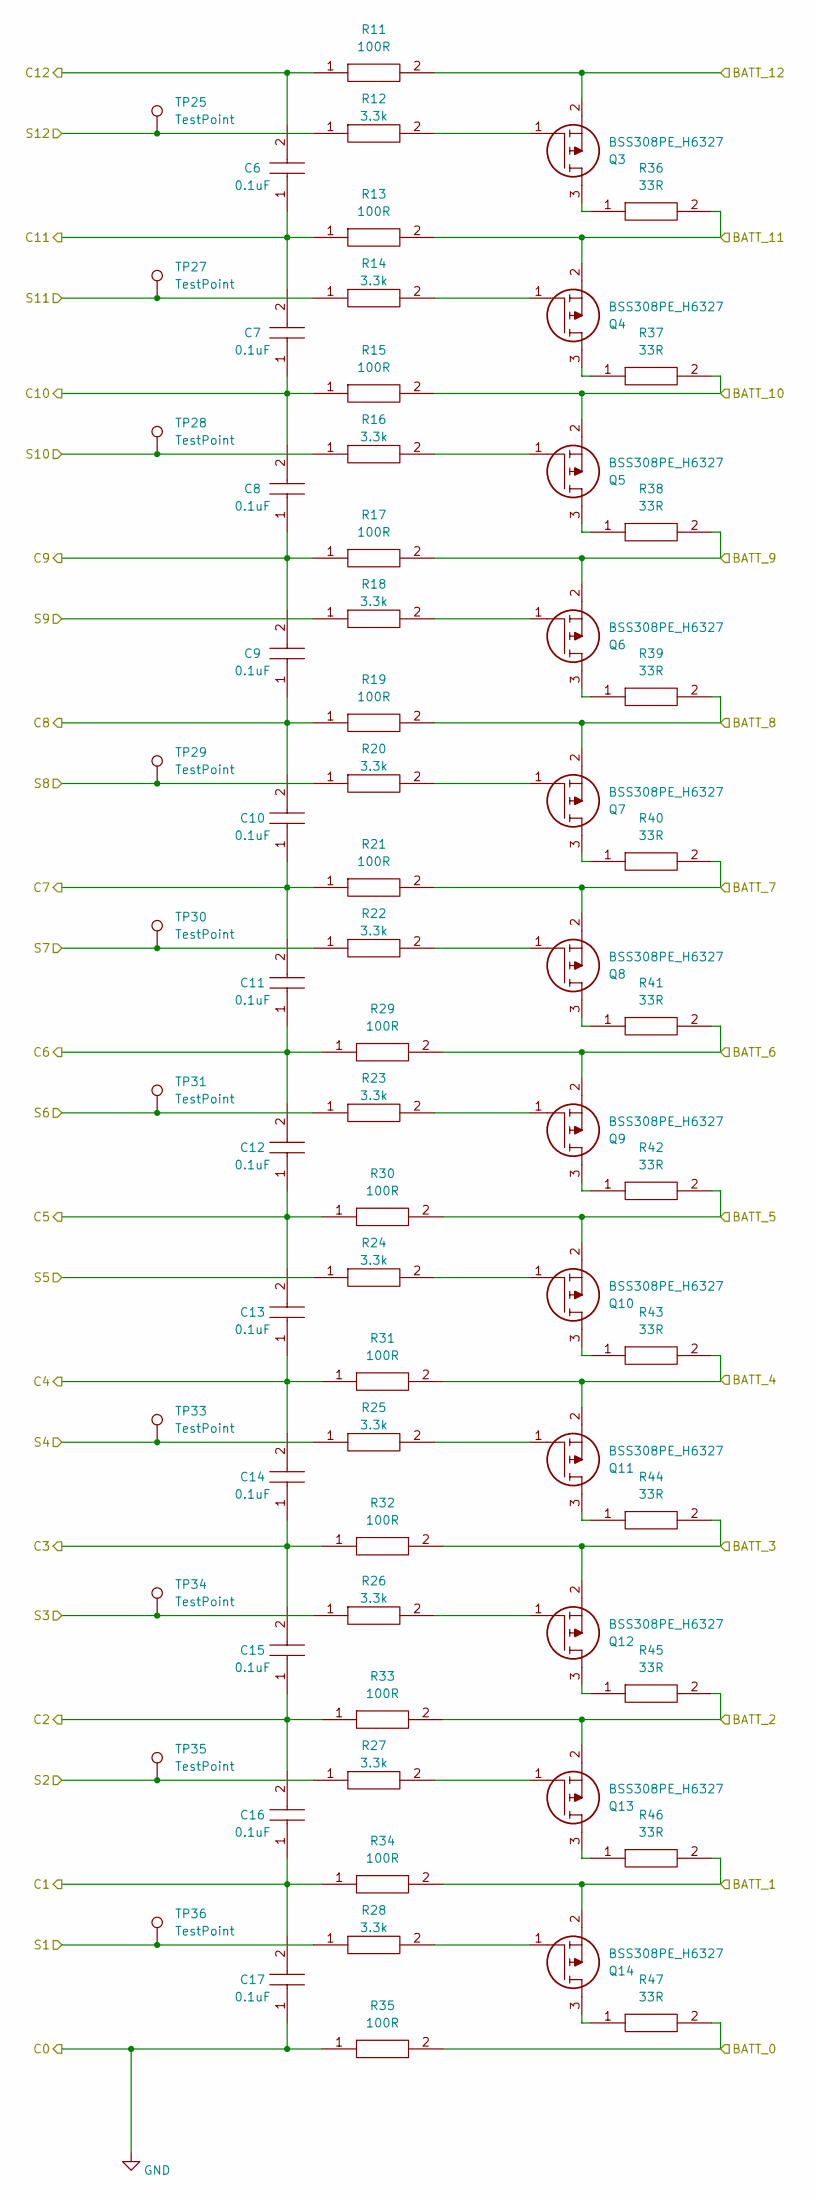
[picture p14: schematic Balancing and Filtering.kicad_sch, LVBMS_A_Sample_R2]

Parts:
C6, C7, C8, C9, C10, C11, C12, C13, C14, C15, C16, C17: 0.1uF; C_0603_1608Metric_Pad1.08x0.95mm_HandSolder; Manufacturer_Part_Number CC0805JRX7R9BB103
Q3, Q4, Q5, Q6, Q7, Q8, Q9, Q10, Q11, Q12, Q13, Q14: BSS308PE_H6327; SOT95P260X110-3N; Manufacturer_Part_Number BSS308PE H6327; Mouser Part Number 726-BSS308PEH6327
R11, R13, R15, R17, R19, R21, R29, R30, R31, R32, R33, R34, R35: 100R; R_0603_1608Metric_Pad0.98x0.95mm_HandSolder; Manufacturer_Part_Number ERJP06F1000V
R12, R14, R16, R18, R20, R22, R23, R24, R25, R26, R27, R28: 3.3k; R_0603_1608Metric_Pad0.98x0.95mm_HandSolder; Manufacturer_Part_Number ERJP06J332V
R36, R37, R38, R39, R40, R41, R42, R43, R44, R45, R46, R47: 33R; R_1206_3216Metric_Pad1.30x1.75mm_HandSolder; Manufacturer_Part_Number ERJ-P6WF33R0V; Mouser Part Number 667-ERJ-P6WF33R0V
TP25, TP27, TP28, TP29, TP30, TP31, TP33, TP34, TP35, TP36: TestPoint; TestPoint_Pad_D1.0mm

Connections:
/Balancing and Filtering/BATT_0: R35.2, R47.2; also elsewhere on the board
/Balancing and Filtering/BATT_1: Q14.2, R34.2, R46.2; also elsewhere on the board
/Balancing and Filtering/BATT_2: Q13.2, R33.2, R45.2; also elsewhere on the board
/Balancing and Filtering/BATT_3: Q12.2, R32.2, R44.2; also elsewhere on the board
/Balancing and Filtering/BATT_4: Q11.2, R31.2, R43.2; also elsewhere on the board
/Balancing and Filtering/BATT_5: Q10.2, R30.2, R42.2; also elsewhere on the board
/Balancing and Filtering/BATT_6: Q9.2, R29.2, R41.2; also elsewhere on the board
/Balancing and Filtering/BATT_7: Q8.2, R21.2, R40.2; also elsewhere on the board
/Balancing and Filtering/BATT_8: Q7.2, R19.2, R39.2; also elsewhere on the board
/Balancing and Filtering/BATT_9: Q6.2, R17.2, R38.2; also elsewhere on the board
/Balancing and Filtering/BATT_10: Q5.2, R15.2, R37.2; also elsewhere on the board
/Balancing and Filtering/BATT_11: Q4.2, R13.2, R36.2; also elsewhere on the board
/Balancing and Filtering/BATT_12: Q3.2, R11.2; also elsewhere on the board
/C1: C16.1, C17.2, R34.1; also elsewhere on the board
/C2: C15.1, C16.2, R33.1; also elsewhere on the board
/C3: C14.1, C15.2, R32.1; also elsewhere on the board
/C4: C13.1, C14.2, R31.1; also elsewhere on the board
/C5: C12.1, C13.2, R30.1; also elsewhere on the board
/C6: C11.1, C12.2, R29.1; also elsewhere on the board
/C7: C10.1, C11.2, R21.1; also elsewhere on the board
/C8: C9.1, C10.2, R19.1; also elsewhere on the board
/C9: C8.1, C9.2, R17.1; also elsewhere on the board
/C10: C7.1, C8.2, R15.1; also elsewhere on the board
/C11: C6.1, C7.2, R13.1; also elsewhere on the board
/C12: C6.2, R11.1; also elsewhere on the board
/S1: R28.1, TP36.1; also elsewhere on the board
/S2: R27.1, TP35.1; also elsewhere on the board
/S3: R26.1, TP34.1; also elsewhere on the board
/S4: R25.1, TP33.1; also elsewhere on the board
/S5: R24.1; also elsewhere on the board
/S6: R23.1, TP31.1; also elsewhere on the board
/S7: R22.1, TP30.1; also elsewhere on the board
/S8: R20.1, TP29.1; also elsewhere on the board
/S9: R18.1; also elsewhere on the board
/S10: R16.1, TP28.1; also elsewhere on the board
/S11: R14.1, TP27.1; also elsewhere on the board
/S12: R12.1, TP25.1; also elsewhere on the board
GND: C17.1, R35.1; also elsewhere on the board
unnamed: Q3.1, R12.2
unnamed: Q3.3, R36.1
unnamed: Q4.1, R14.2
unnamed: Q4.3, R37.1
unnamed: Q5.1, R16.2
unnamed: Q5.3, R38.1
unnamed: Q6.1, R18.2
unnamed: Q6.3, R39.1
unnamed: Q7.1, R20.2
unnamed: Q7.3, R40.1
unnamed: Q8.1, R22.2
unnamed: Q8.3, R41.1
unnamed: Q9.1, R23.2
unnamed: Q9.3, R42.1
unnamed: Q10.1, R24.2
unnamed: Q10.3, R43.1
unnamed: Q11.1, R25.2
unnamed: Q11.3, R44.1
unnamed: Q12.1, R26.2
unnamed: Q12.3, R45.1
unnamed: Q13.1, R27.2
unnamed: Q13.3, R46.1
unnamed: Q14.1, R28.2
unnamed: Q14.3, R47.1

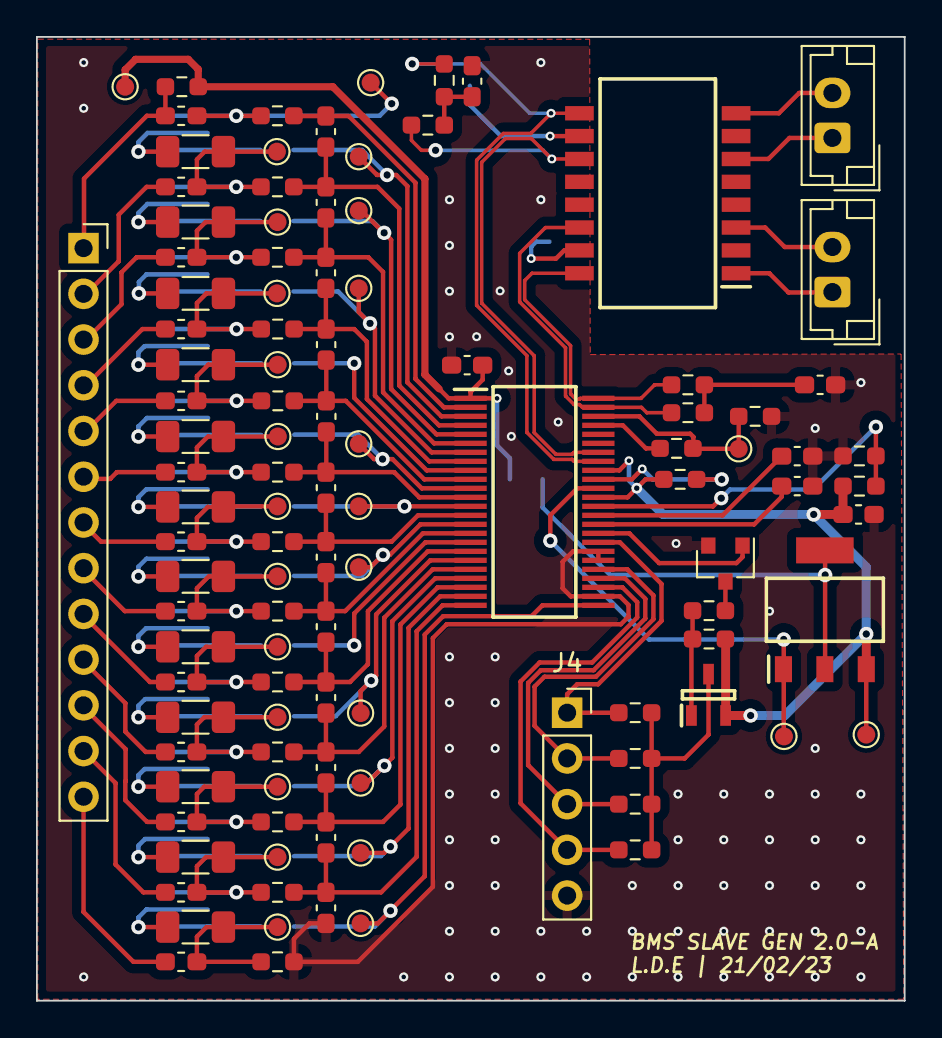
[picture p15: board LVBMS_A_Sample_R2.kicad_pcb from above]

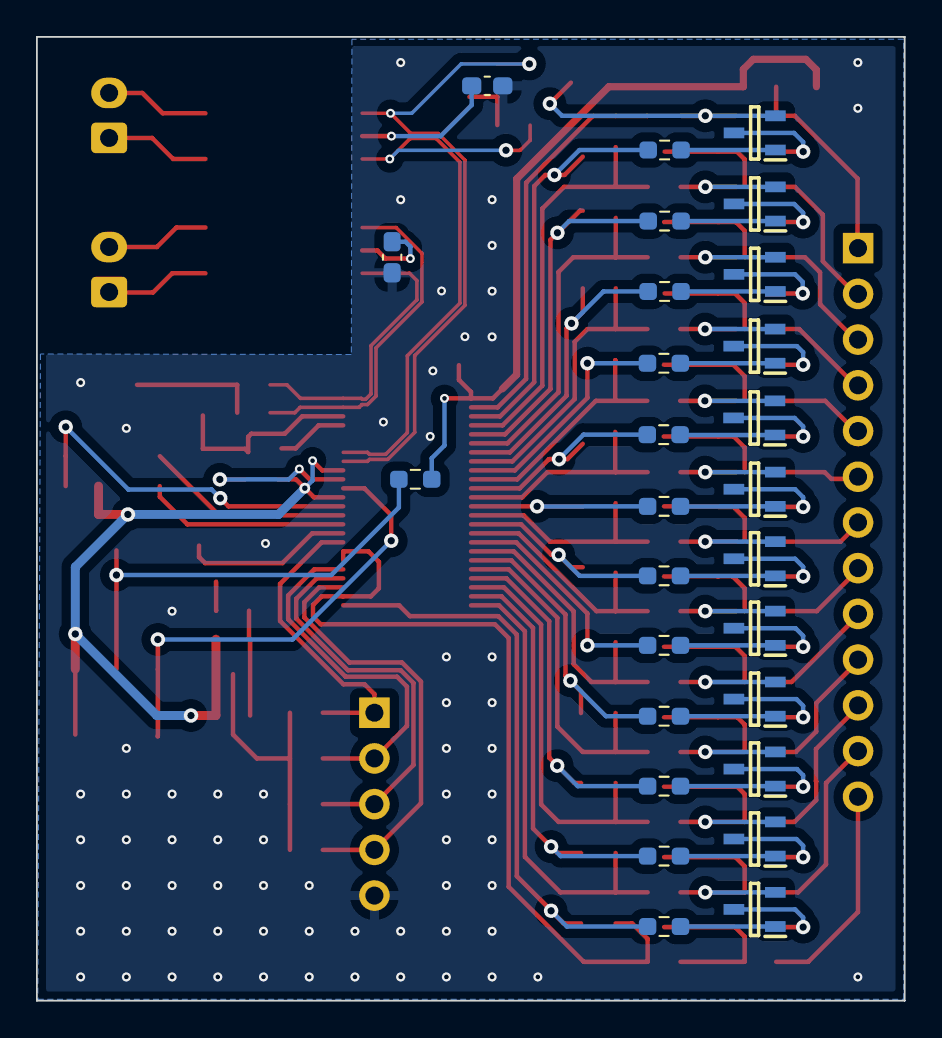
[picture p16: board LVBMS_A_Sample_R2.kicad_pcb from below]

Board: 2 copper layers, 48.2 x 53.5 mm, 135 parts (27 on the bottom side), 105 nets.

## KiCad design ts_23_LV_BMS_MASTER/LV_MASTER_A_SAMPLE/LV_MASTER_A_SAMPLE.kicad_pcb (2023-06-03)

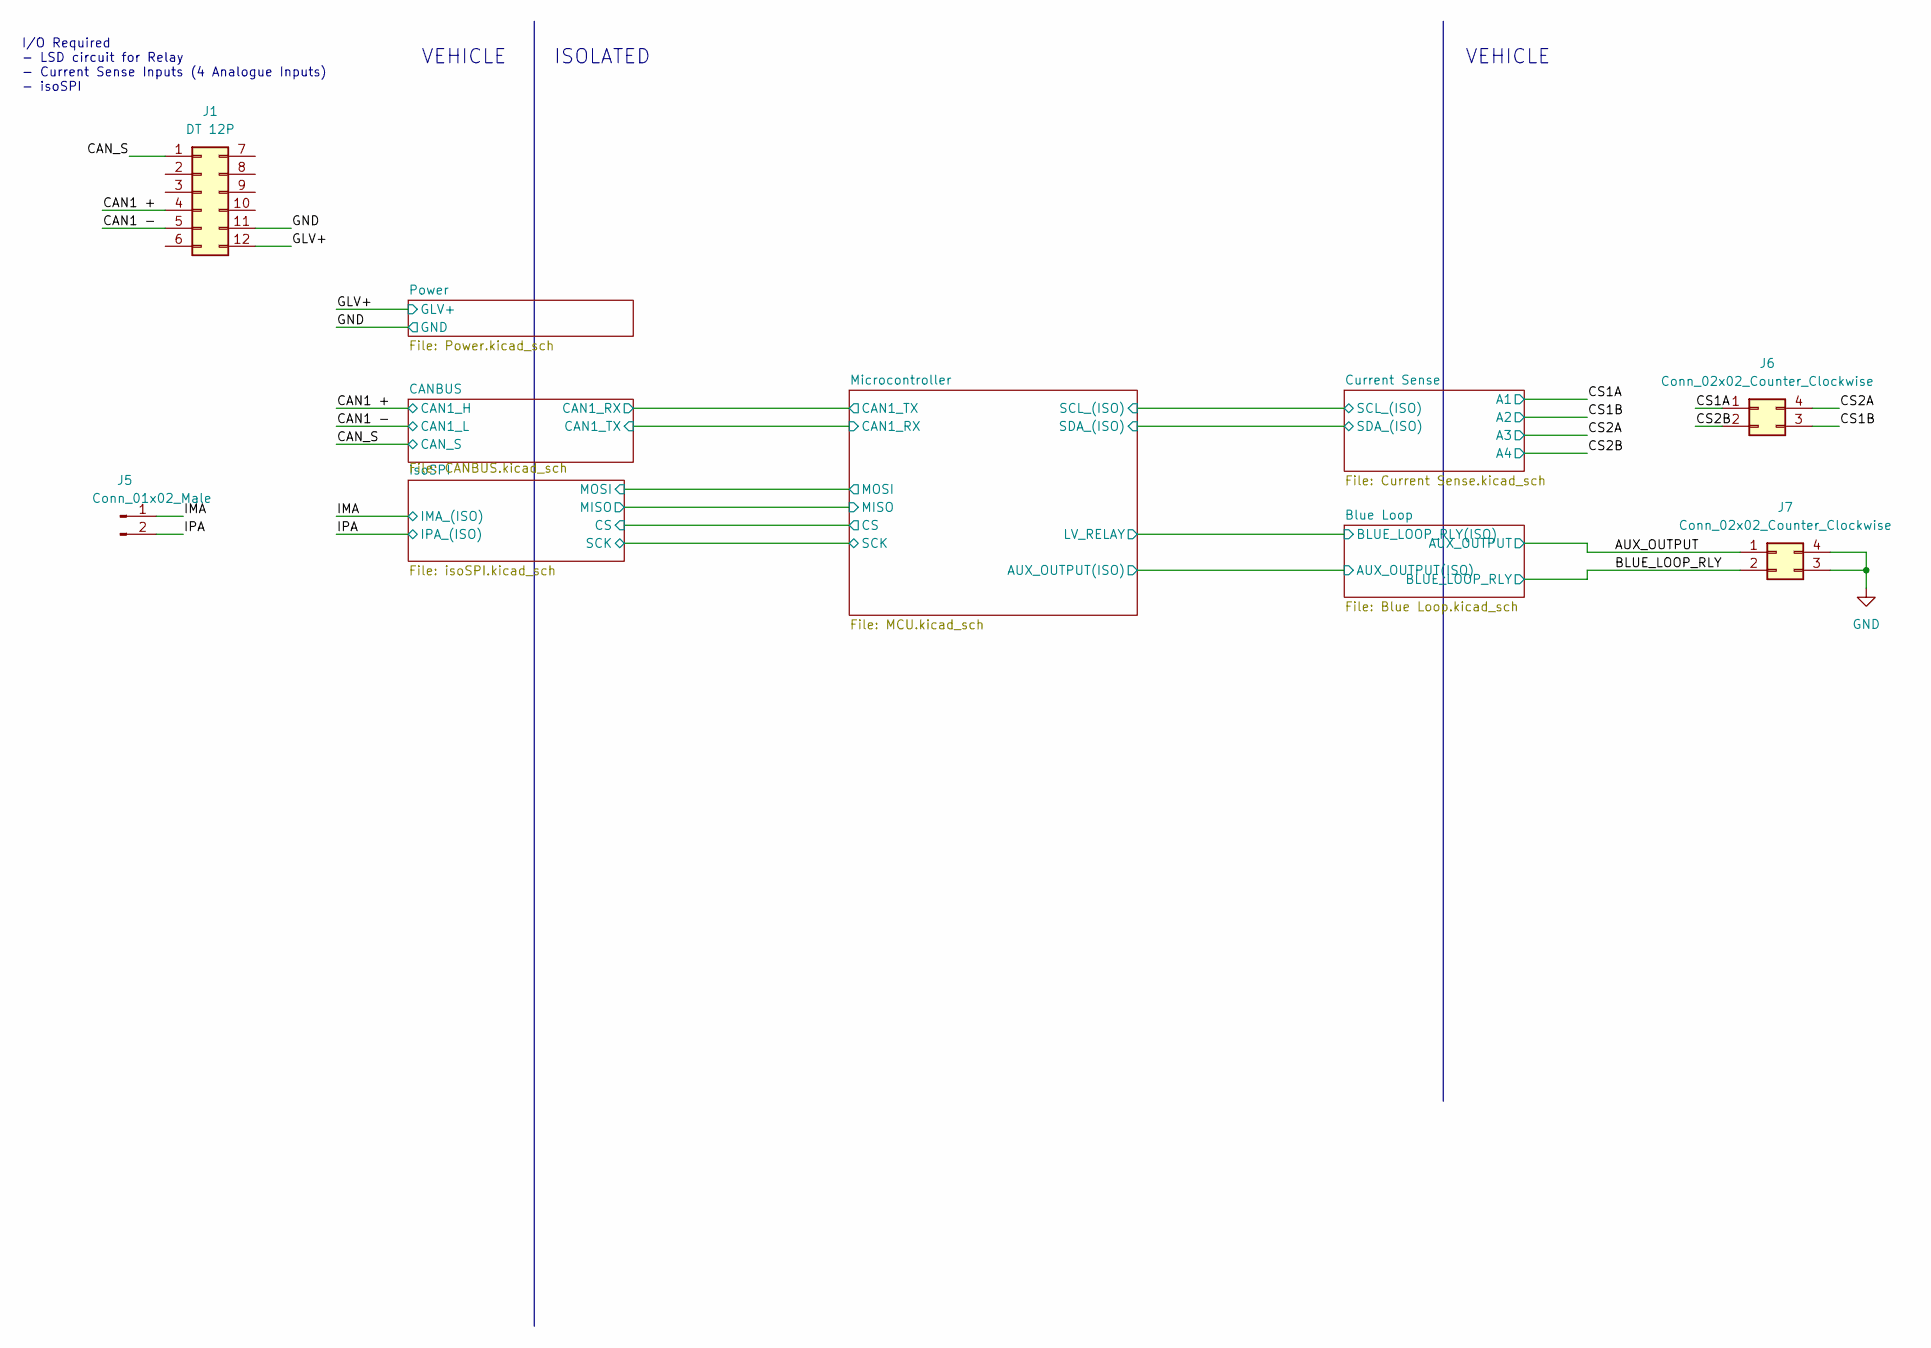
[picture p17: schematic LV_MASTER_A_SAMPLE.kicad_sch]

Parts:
J1: DT 12P; DT12-PCB PIN
J5: Conn_01x02_Male; Molex_Mini-Fit_Jr_5566-02A_2x01_P4.20mm_Vertical
J6, J7: Conn_02x02_Counter_Clockwise; Molex_Mini-Fit_Jr_5566-04A_2x02_P4.20mm_Vertical

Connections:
/AUX_OUTPUT: J7.1; also elsewhere on the board
/BLUE_LOOP_RLY: J7.2; also elsewhere on the board
/CAN1 +: J1.4; also elsewhere on the board
/CAN1 -: J1.5; also elsewhere on the board
/CS1A: J6.1; also elsewhere on the board
/CS1B: J6.3; also elsewhere on the board
/CS2A: J6.4; also elsewhere on the board
/CS2B: J6.2; also elsewhere on the board
/GLV+: J1.12; also elsewhere on the board
/IMA: J5.1; also elsewhere on the board
/IPA: J5.2; also elsewhere on the board
GND: J1.1, J1.11, J7.3, J7.4; also elsewhere on the board

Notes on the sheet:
I/O Required - LSD circuit for Relay - Current Sense Inputs (4 Analogue Inputs) - isoSPI
VEHICLE
ISOLATED

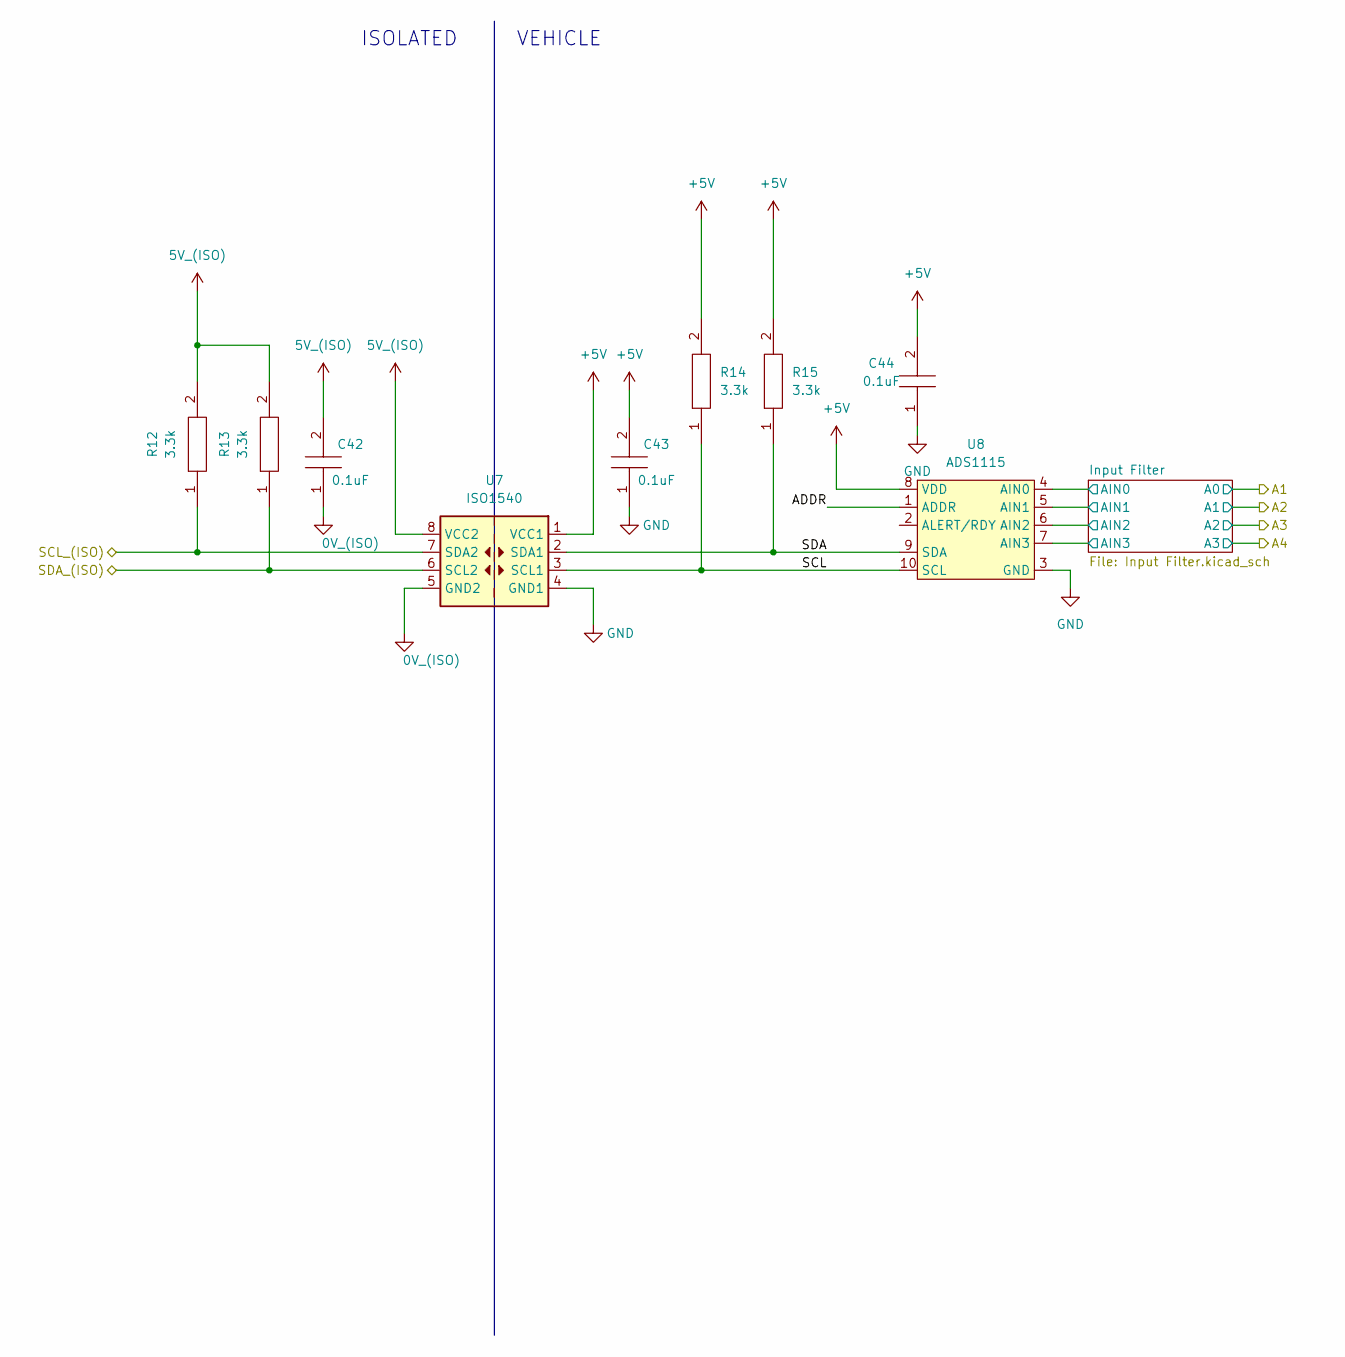
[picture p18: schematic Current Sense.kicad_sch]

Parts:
C42, C43, C44: 0.1uF; C_0603_1608Metric_Pad1.08x0.95mm_HandSolder; Manufacturer_Part_Number CC0805JRX7R8BB104; Mouser Part Number 603-CC805JRX7R8BB104
R12, R13, R14, R15: 3.3k; R_0603_1608Metric_Pad0.98x0.95mm_HandSolder; Manufacturer_Part_Number ERJP06F1000V
U7: ISO1540; SOIC-8_3.9x4.9mm_P1.27mm
U8: ADS1115; VSSOP-10_3x3mm_P0.5mm

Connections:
0V_(ISO): C42.1, U7.5 (GND2); also elsewhere on the board
5V_(ISO): C42.2, R12.2, R13.2, U7.8 (VCC2); also elsewhere on the board
+5V: C43.2, C44.2, R14.2, R15.2, U7.1 (VCC1), U8.8 (VDD); also elsewhere on the board
/Current Sense/ADDR: U8.1 (ADDR)
/Current Sense/Input Filter/AIN0: U8.4 (AIN0); also elsewhere on the board
/Current Sense/Input Filter/AIN1: U8.5 (AIN1); also elsewhere on the board
/Current Sense/Input Filter/AIN2: U8.6 (AIN2); also elsewhere on the board
/Current Sense/Input Filter/AIN3: U8.7 (AIN3); also elsewhere on the board
/Current Sense/SCL: R14.1, U7.3 (SCL1), U8.10 (SCL)
/Current Sense/SDA: R15.1, U7.2 (SDA1), U8.9 (SDA)
/Microcontroller/SCL_(ISO): R12.1, U7.7 (SDA2); also elsewhere on the board
/Microcontroller/SDA_(ISO): R13.1, U7.6 (SCL2); also elsewhere on the board
GND: C43.1, C44.1, U7.4 (GND1), U8.3 (GND); also elsewhere on the board

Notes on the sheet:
ISOLATED
VEHICLE

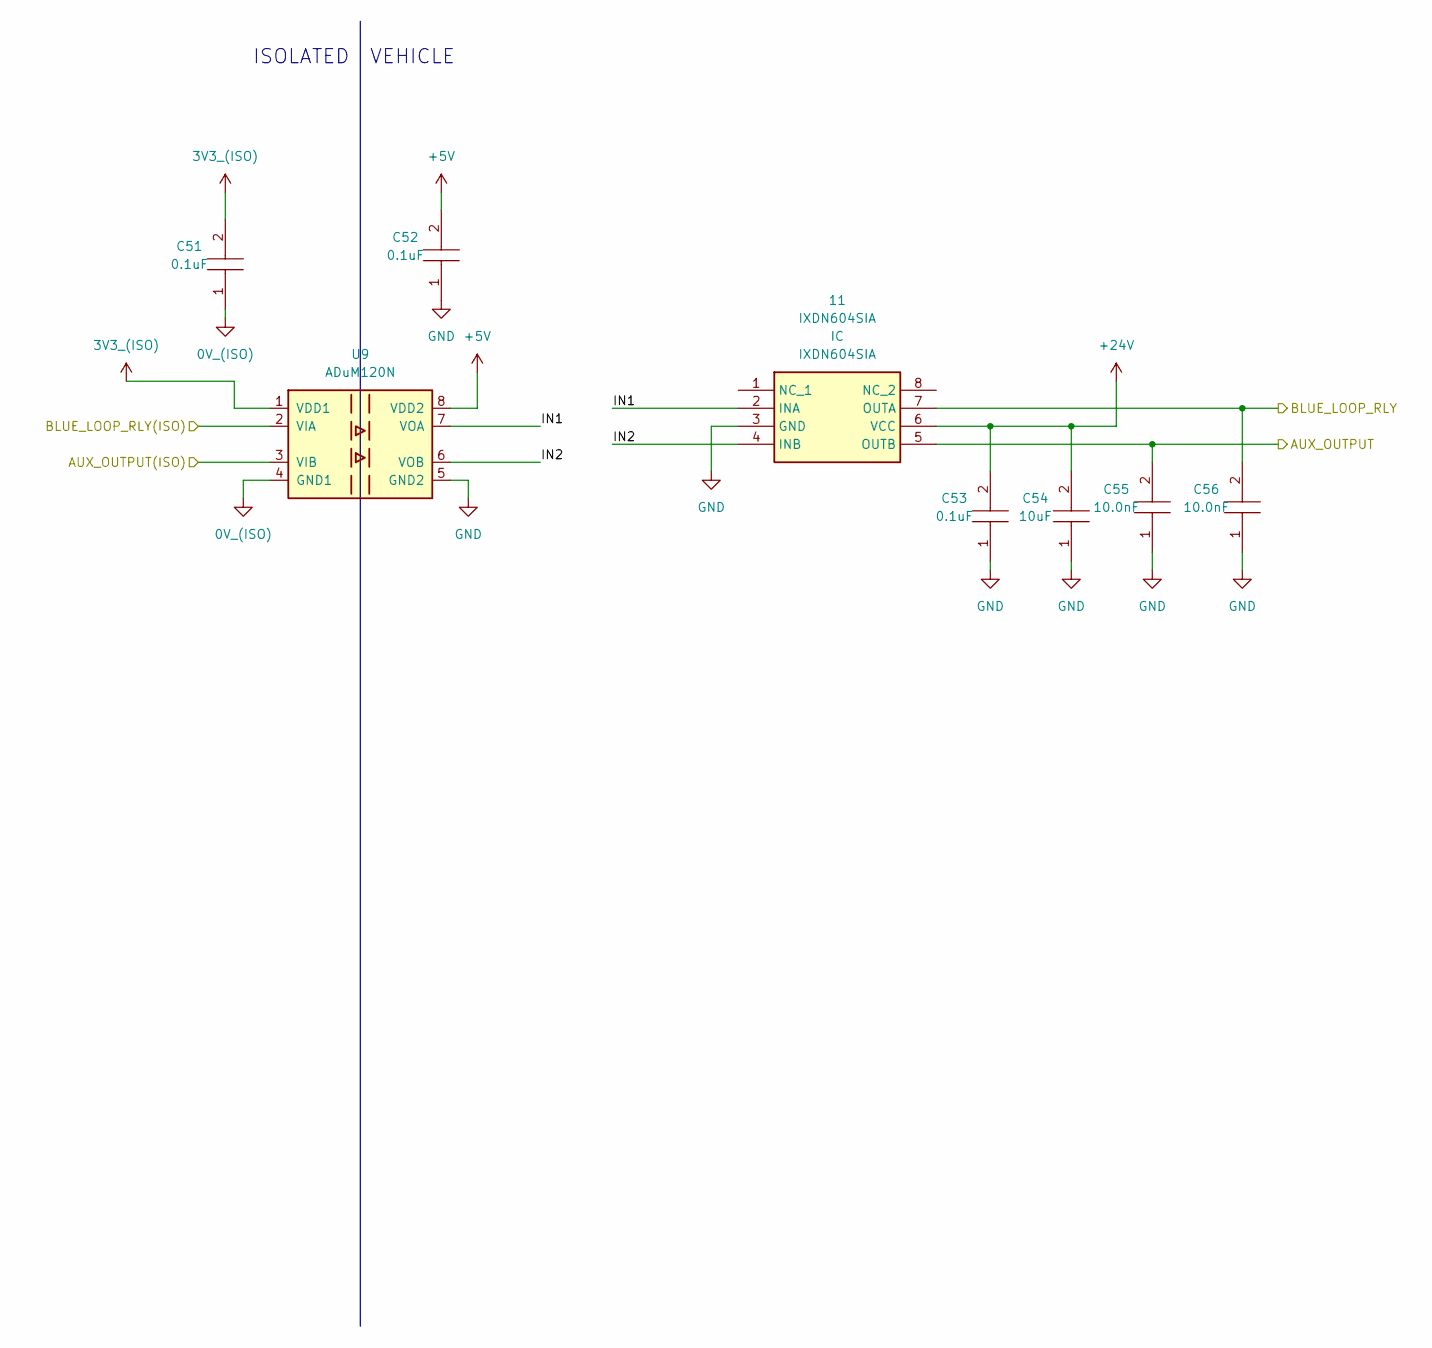
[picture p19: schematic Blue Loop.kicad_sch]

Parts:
11: IXDN604SIA; SOIC127P600X175-8N; Manufacturer_Part_Number IXDN604SIA; Mouser Part Number 849-IXDN604SIA
C51, C52, C53: 0.1uF; C_0603_1608Metric_Pad1.08x0.95mm_HandSolder; Manufacturer_Part_Number CC0805JRX7R8BB104; Mouser Part Number 603-CC805JRX7R8BB104
C54: 10uF; C_0603_1608Metric_Pad1.08x0.95mm_HandSolder; Manufacturer_Part_Number CC0805JRX7R8BB104; Mouser Part Number 603-CC805JRX7R8BB104
C55, C56: 10.0nF; C_0603_1608Metric_Pad1.08x0.95mm_HandSolder; Manufacturer_Part_Number CC0805JRX7R8BB104; Mouser Part Number 603-CC805JRX7R8BB104
U9: ADuM120N; SOIC-8_3.9x4.9mm_P1.27mm

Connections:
0V_(ISO): C51.1, U9.4 (GND1); also elsewhere on the board
+3.3V: C51.2, U9.1 (VDD1)
+5V: C52.2, U9.8 (VDD2); also elsewhere on the board
+24V: 11.6 (VCC), C53.2, C54.2; also elsewhere on the board
/AUX_OUTPUT: 11.5 (OUTB), C55.2; also elsewhere on the board
/BLUE_LOOP_RLY: 11.7 (OUTA), C56.2; also elsewhere on the board
/Blue Loop/AUX_OUTPUT(ISO): U9.3 (VIB); also elsewhere on the board
/Blue Loop/BLUE_LOOP_RLY(ISO): U9.2 (VIA); also elsewhere on the board
/Blue Loop/IN1: 11.2 (INA), U9.7 (VOA)
/Blue Loop/IN2: 11.4 (INB), U9.6 (VOB)
GND: 11.3 (GND), C52.1, C53.1, C54.1, C55.1, C56.1, U9.5 (GND2); also elsewhere on the board

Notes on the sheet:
VEHICLE
ISOLATED

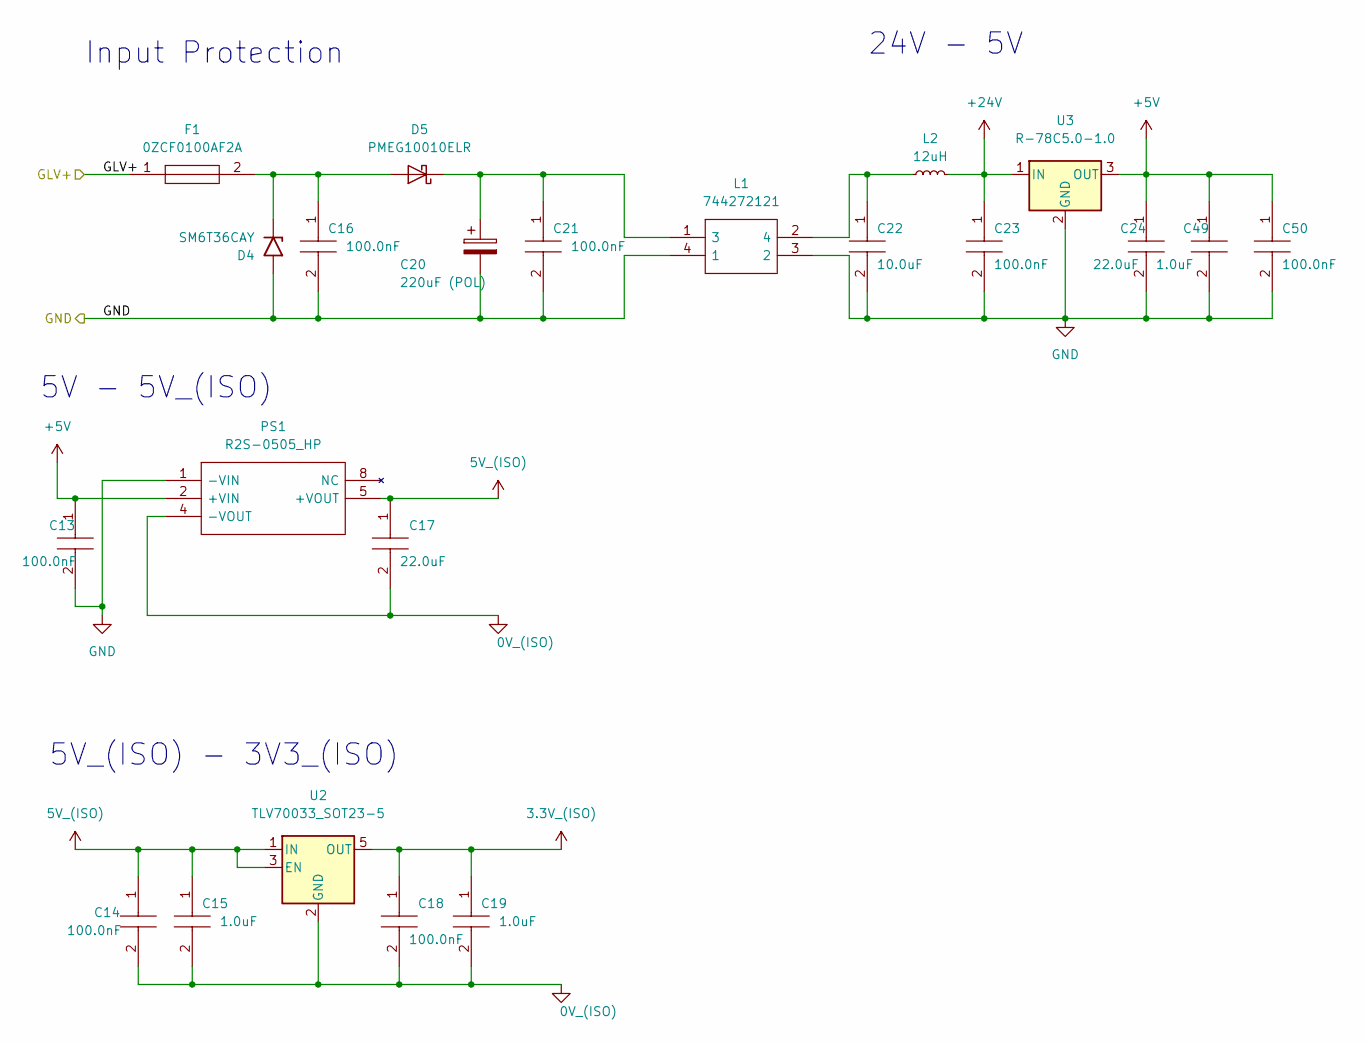
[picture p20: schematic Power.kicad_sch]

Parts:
C13, C14, C18, C21, C23, C50: 100.0nF; C_0603_1608Metric_Pad1.08x0.95mm_HandSolder; Manufacturer_Part_Number CC0805JRX7R8BB104; Mouser Part Number 603-CC805JRX7R8BB104
C15, C19, C49: 1.0uF; C_0603_1608Metric_Pad1.08x0.95mm_HandSolder; Manufacturer_Part_Number CC0805JRX7R8BB104; Mouser Part Number 603-CC805JRX7R8BB104
C16: 100.0nF; C_0805_2012Metric_Pad1.18x1.45mm_HandSolder; Manufacturer_Part_Number CC0805JRX7R8BB104; Mouser Part Number 603-CC805JRX7R8BB104
C17, C24: 22.0uF; C_0805_2012Metric_Pad1.18x1.45mm_HandSolder; Manufacturer_Part_Number CC0805JRX7R8BB104; Mouser Part Number 603-CC805JRX7R8BB104
C20: 220uF (POL); TLV_10X10.5_
C22: 10.0uF; C_0603_1608Metric_Pad1.08x0.95mm_HandSolder; Manufacturer_Part_Number CC0805JRX7R8BB104; Mouser Part Number 603-CC805JRX7R8BB104
D4: SM6T36CAY; D_SMB
D5: PMEG10010ELR; Nexperia_CFP3_SOD-123W
F1: 0ZCF0100AF2A; FUSC7451X170N; Manufacturer_Part_Number 0ZCF0100AF2A; Mouser Part Number 530-0ZCF0100AF2A
L1: 744272121; WE-SL575; Manufacturer_Part_Number 744272121; Mouser Part Number 710-744272121
L2: 12uH; L_1210_3225Metric_Pad1.42x2.65mm_HandSolder
PS1: R2S-0505_HP; R2S0505HP; Manufacturer_Part_Number R2S-0505/HP; Mouser Part Number 919-R2S-0505HP
U2: TLV70033_SOT23-5; SOT-23-5
U3: R-78C5.0-1.0; Converter_DCDC_RECOM_R-78E-0.5_THT

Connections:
0V_(ISO): C14.2, C15.2, C17.2, C18.2, C19.2, PS1.4 (-VOUT), U2.2 (GND); also elsewhere on the board
3.3V_(ISO): C18.1, C19.1, U2.5 (OUT); also elsewhere on the board
5V_(ISO): C14.1, C15.1, C17.1, PS1.5 (+VOUT), U2.1 (IN), U2.3 (EN); also elsewhere on the board
+5V: C13.1, C24.1, C49.1, C50.1, PS1.2 (+VIN), U3.3 (OUT); also elsewhere on the board
+24V: C23.1, L2.2, U3.1 (IN); also elsewhere on the board
/GLV+: F1.1; also elsewhere on the board
GND: C13.2, C16.2, C20.2, C21.2, C22.2, C23.2, C24.2, C49.2, C50.2, D4.2 (A2), L1.3 (2), L1.4 (1), PS1.1 (-VIN), U3.2 (GND); also elsewhere on the board
unnamed: C16.1, D4.1 (A1), D5.2 (A), F1.2
unnamed: C20.1, C21.1, D5.1 (K), L1.1 (3)
unnamed: C22.1, L1.2 (4), L2.1

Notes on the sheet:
5V_(ISO) - 3V3_(ISO)
Input Protection
5V - 5V_(ISO)
24V - 5V

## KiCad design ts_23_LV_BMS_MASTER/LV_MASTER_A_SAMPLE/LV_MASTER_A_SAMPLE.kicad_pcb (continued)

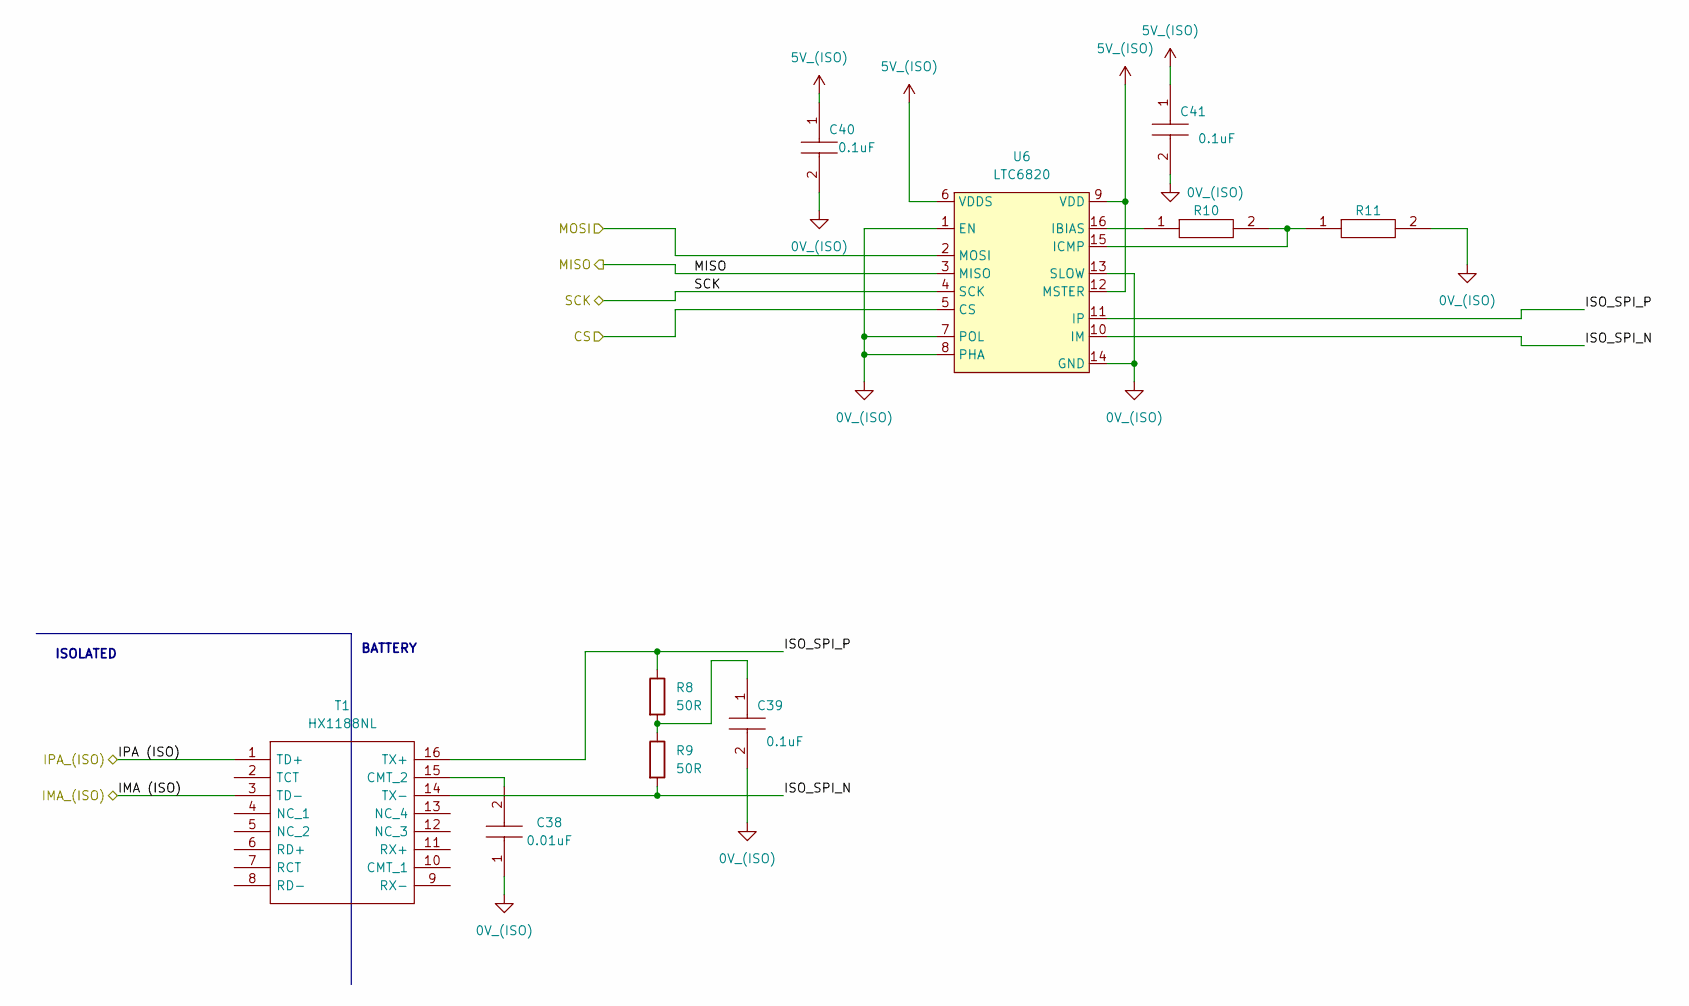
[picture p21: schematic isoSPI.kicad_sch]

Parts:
C38: 0.01uF; C_0603_1608Metric_Pad1.08x0.95mm_HandSolder; Manufacturer_Part_Number CC0805JRX7R9BB103
C39, C40, C41: 0.1uF; C_0603_1608Metric_Pad1.08x0.95mm_HandSolder; Manufacturer_Part_Number CC0805JRX7R8BB104; Mouser Part Number 603-CC805JRX7R8BB104
R8, R9: 50R; R_0603_1608Metric_Pad0.98x0.95mm_HandSolder
R10, R11: ERJP06F1000V; R_0603_1608Metric_Pad0.98x0.95mm_HandSolder; Manufacturer_Part_Number ERJP06F1000V
T1: HX1188NL; SOIC127P940X597-16N; Manufacturer_Part_Number HX1188NL; Mouser Part Number 673-HX1188NL
U6: LTC6820; MSOP-16_3x4.039mm_P0.5mm

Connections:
0V_(ISO): C38.1, C39.2, C40.2, C41.2, R11.2, U6.1 (EN), U6.7 (POL), U6.8 (PHA), U6.13 (SLOW), U6.14 (GND); also elsewhere on the board
5V_(ISO): C40.1, C41.1, U6.6 (VDDS), U6.9 (VDD), U6.12 (MSTER); also elsewhere on the board
/IMA: T1.3 (TD-); also elsewhere on the board
/IPA: T1.1 (TD+); also elsewhere on the board
/Microcontroller/CS: U6.5 (CS); also elsewhere on the board
/Microcontroller/MISO: U6.3 (MISO); also elsewhere on the board
/Microcontroller/MOSI: U6.2 (MOSI); also elsewhere on the board
/Microcontroller/SCK: U6.4 (SCK); also elsewhere on the board
/isoSPI/ISO_SPI_N: R9.2, T1.14 (TX-), U6.10 (IM)
/isoSPI/ISO_SPI_P: R8.1, T1.16 (TX+), U6.11 (IP)
unnamed: C38.2, T1.15 (CMT_2)
unnamed: C39.1, R8.2, R9.1
unnamed: R10.1, U6.16 (IBIAS)
unnamed: R10.2, R11.1, U6.15 (ICMP)

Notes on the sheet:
ISOLATED
BATTERY

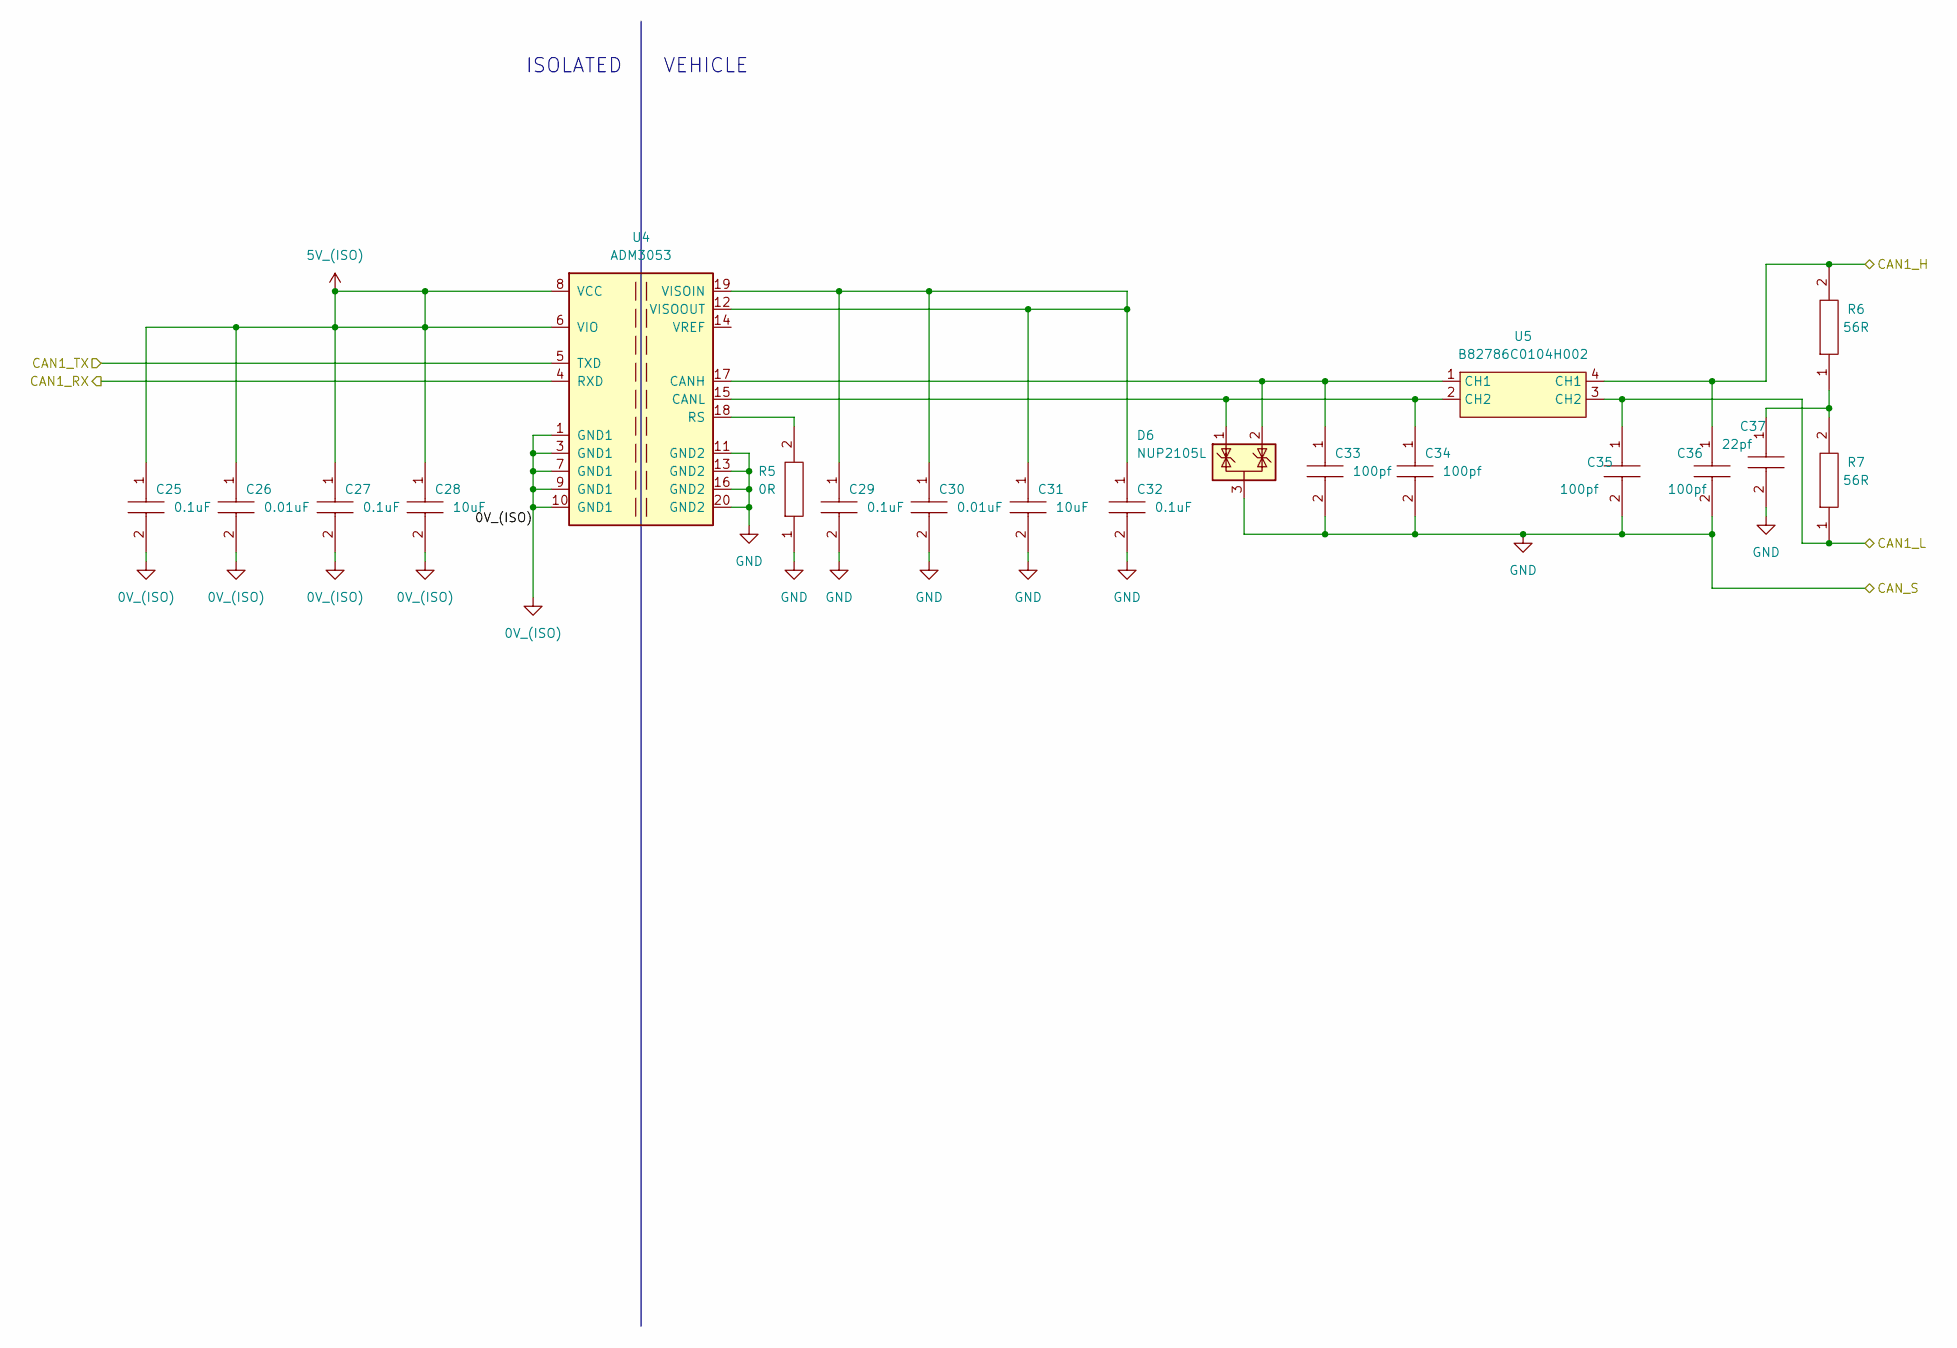
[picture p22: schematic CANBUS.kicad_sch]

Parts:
C25, C27, C29, C32: 0.1uF; C_0603_1608Metric_Pad1.08x0.95mm_HandSolder; Manufacturer_Part_Number CC0805JRX7R8BB104; Mouser Part Number 603-CC805JRX7R8BB104
C26, C30: 0.01uF; C_0603_1608Metric_Pad1.08x0.95mm_HandSolder; Manufacturer_Part_Number CC0805JRX7R8BB104; Mouser Part Number 603-CC805JRX7R8BB104
C28, C31: 10uF; C_0603_1608Metric_Pad1.08x0.95mm_HandSolder; Manufacturer_Part_Number CC0805JRX7R8BB104; Mouser Part Number 603-CC805JRX7R8BB104
C33, C34, C35, C36: 100pf; C_0603_1608Metric_Pad1.08x0.95mm_HandSolder; Manufacturer_Part_Number CC0805JRX7R8BB104; Mouser Part Number 603-CC805JRX7R8BB104
C37: 22pf; C_0603_1608Metric_Pad1.08x0.95mm_HandSolder; Manufacturer_Part_Number CC0805JRX7R8BB104; Mouser Part Number 603-CC805JRX7R8BB104
D6: NUP2105L; SOT-23
R5: 0R; R_0603_1608Metric_Pad0.98x0.95mm_HandSolder; Manufacturer_Part_Number ERJP06F1000V
R6, R7: 56R; R_0603_1608Metric_Pad0.98x0.95mm_HandSolder; Manufacturer_Part_Number ERJP06F1000V
U4: ADM3053; SOIC-20W_7.5x12.8mm_P1.27mm
U5: B82786C0104H002

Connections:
0V_(ISO): C25.2, C26.2, C27.2, C28.2, U4.1 (GND1), U4.3 (GND1), U4.7 (GND1), U4.9 (GND1), U4.10 (GND1); also elsewhere on the board
5V_(ISO): C25.1, C26.1, C27.1, C28.1, U4.6 (VIO), U4.8 (VCC); also elsewhere on the board
/CAN1 +: C36.1, R6.2, U5.4 (CH1); also elsewhere on the board
/CAN1 -: C35.1, R7.1, U5.3 (CH2); also elsewhere on the board
/CANBUS/CAN1_RX: U4.4 (RXD); also elsewhere on the board
/CANBUS/CAN1_TX: U4.5 (TXD); also elsewhere on the board
GND: C29.2, C30.2, C31.2, C32.2, C33.2, C34.2, C35.2, C36.2, C37.2, D6.3 (A), R5.1, U4.11 (GND2), U4.13 (GND2), U4.16 (GND2), U4.20 (GND2); also elsewhere on the board
unnamed: C29.1, C30.1, C31.1, C32.1, U4.12 (VISOOUT), U4.19 (VISOIN)
unnamed: C33.1, D6.2 (K), U4.17 (CANH), U5.1 (CH1)
unnamed: C34.1, D6.1 (K), U4.15 (CANL), U5.2 (CH2)
unnamed: C37.1, R6.1, R7.2
unnamed: R5.2, U4.18 (RS)

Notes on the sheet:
VEHICLE
ISOLATED

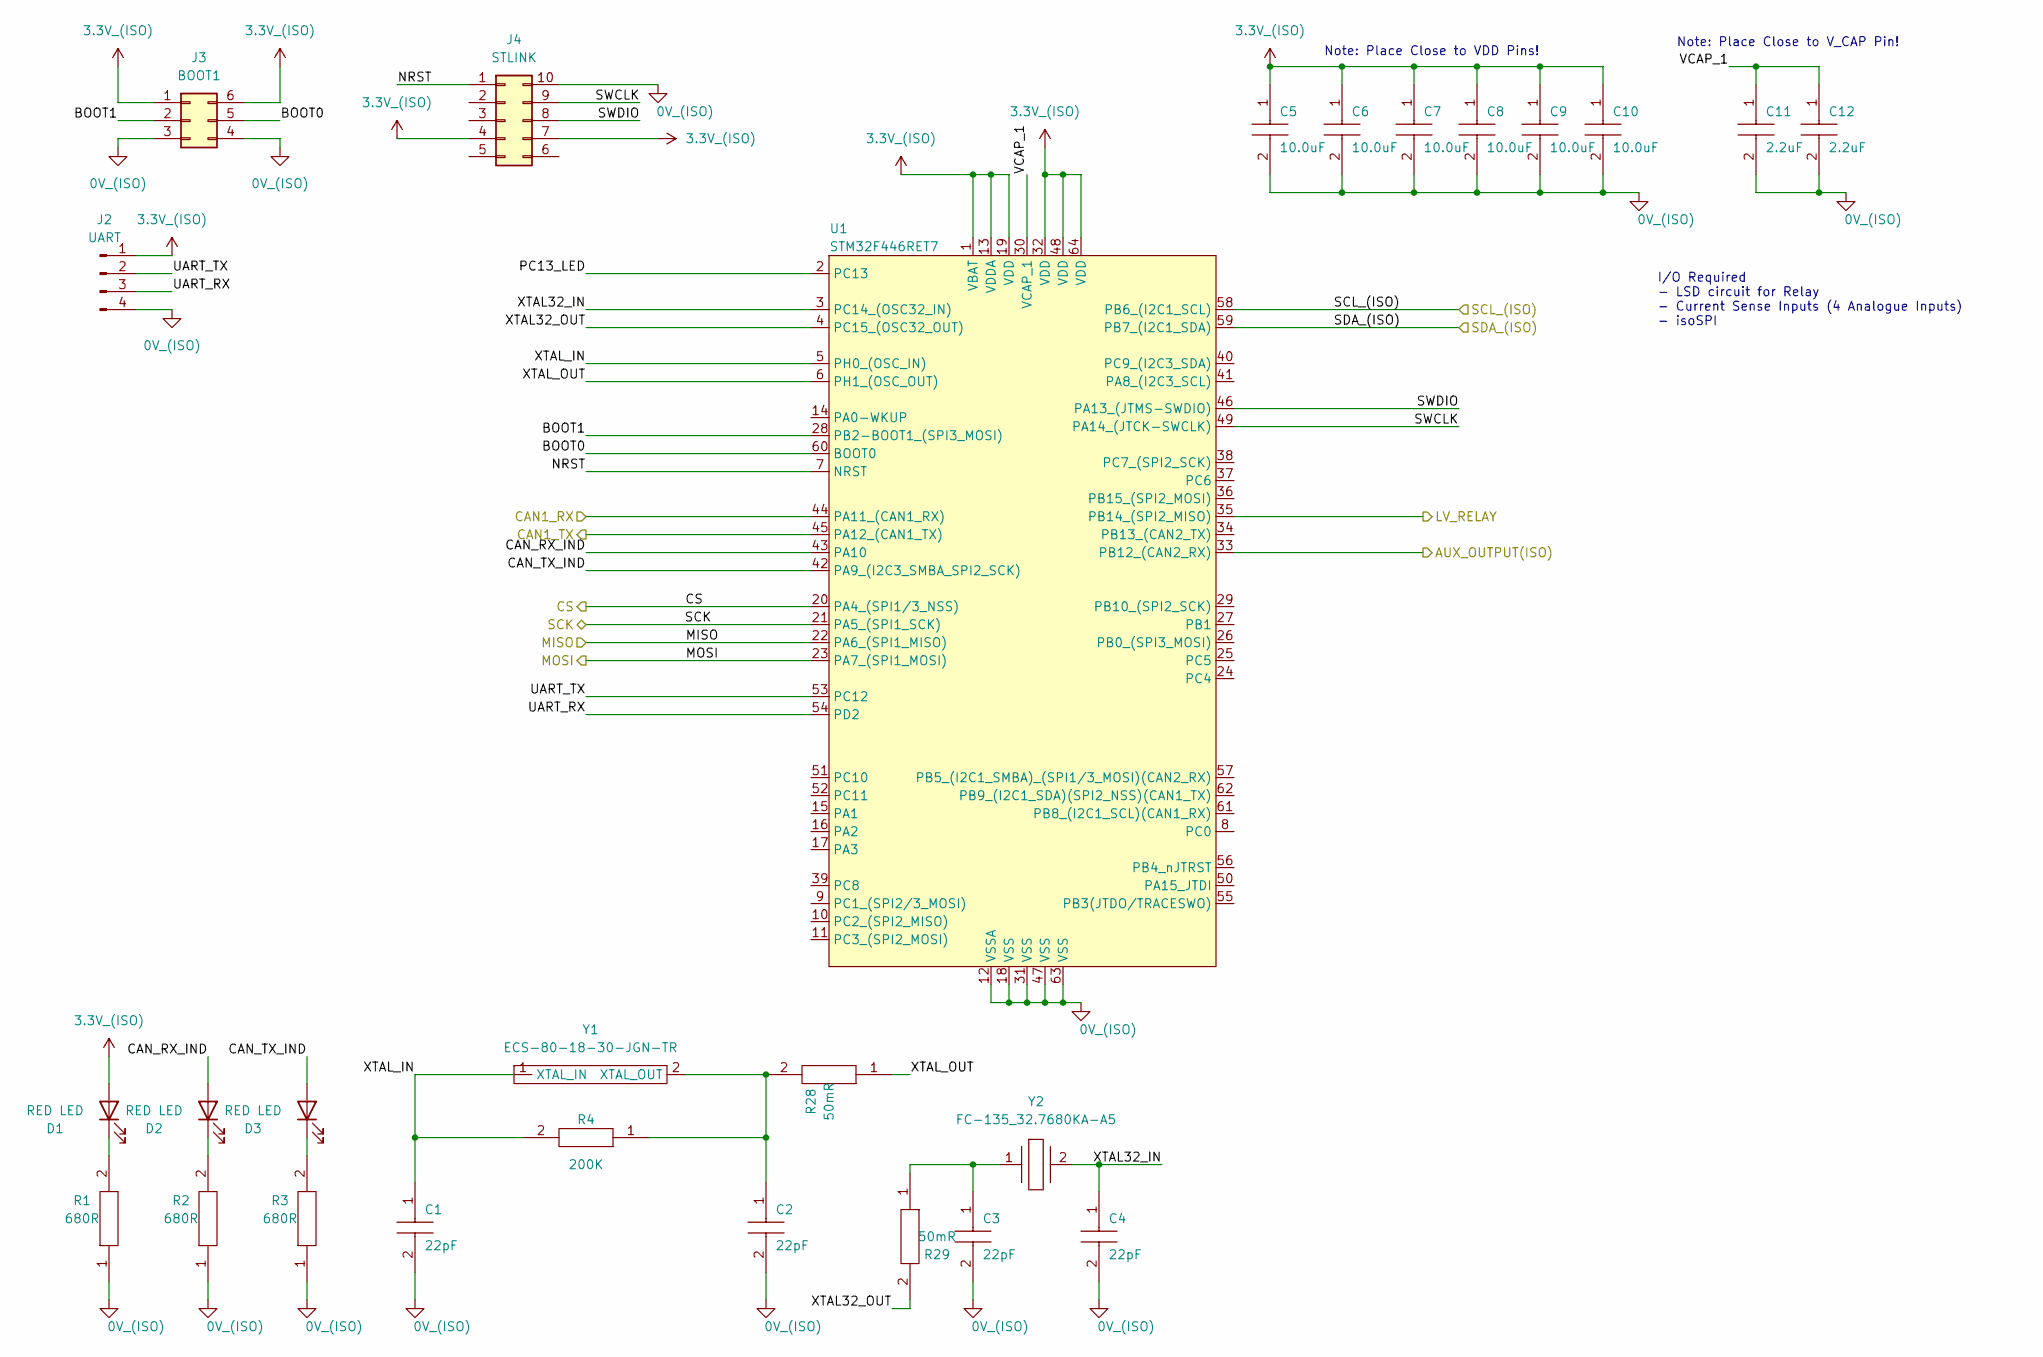
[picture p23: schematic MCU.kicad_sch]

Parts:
C1, C2, C3, C4: 22pF; C_0603_1608Metric_Pad1.08x0.95mm_HandSolder; Manufacturer_Part_Number CC0805JRX7R8BB104; Mouser Part Number 603-CC805JRX7R8BB104
C5, C6, C7, C8, C9, C10: 10.0uF; C_0603_1608Metric_Pad1.08x0.95mm_HandSolder; Manufacturer_Part_Number CC0805JRX7R8BB104; Mouser Part Number 603-CC805JRX7R8BB104
C11, C12: 2.2uF; C_0603_1608Metric_Pad1.08x0.95mm_HandSolder; Manufacturer_Part_Number CC0805JRX7R8BB104; Mouser Part Number 603-CC805JRX7R8BB104
D1, D2, D3: RED LED; C_0805_2012Metric_Pad1.18x1.45mm_HandSolder
J2: UART; PinHeader_1x04_P2.54mm_Vertical
J3: BOOT1; PinSocket_2x03_P2.54mm_Vertical
J4: STLINK; PinSocket_2x05_P2.54mm_Vertical_SMD
R1, R2, R3: 680R; R_0603_1608Metric_Pad0.98x0.95mm_HandSolder; Manufacturer_Part_Number ERJP06F1000V
R4: 200K; R_0603_1608Metric_Pad0.98x0.95mm_HandSolder; Manufacturer_Part_Number ERJP06F1000V
R28, R29: 50mR; R_0603_1608Metric_Pad0.98x0.95mm_HandSolder; Manufacturer_Part_Number ERJP06F1000V
U1: STM32F446RET7; LQFP-64_10x10mm_P0.5mm
Y1: ECS-80-18-30-JGN-TR
Y2: FC-135_32.7680KA-A5; FC135327680KAA5; Manufacturer_Part_Number FC-135 32.7680KA-A5; Mouser Part Number 732-532.7680KA-A5

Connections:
0V_(ISO): C1.2, C2.2, C3.2, C4.2, C5.2, C6.2, C7.2, C8.2, C9.2, C10.2, C11.2, C12.2, J2.4, J3.3, J3.4, J4.10, R1.1, R2.1, R3.1, U1.12 (VSSA), U1.18 (VSS), U1.31 (VSS), U1.47 (VSS), U1.63 (VSS); also elsewhere on the board
3.3V_(ISO): C5.1, C6.1, C7.1, C8.1, C9.1, C10.1, D1.2 (A), J2.1, J3.1, J3.6, J4.4, J4.7, U1.1 (VBAT), U1.13 (VDDA), U1.19 (VDD), U1.32 (VDD), U1.48 (VDD), U1.64 (VDD); also elsewhere on the board
/Blue Loop/AUX_OUTPUT(ISO): U1.33 (PB12_(CAN2_RX)); also elsewhere on the board
/Blue Loop/BLUE_LOOP_RLY(ISO): U1.35 (PB14_(SPI2_MISO)); also elsewhere on the board
/CANBUS/CAN1_RX: U1.45 (PA12_(CAN1_TX)); also elsewhere on the board
/CANBUS/CAN1_TX: U1.44 (PA11_(CAN1_RX)); also elsewhere on the board
/Microcontroller/BOOT0: J3.5, U1.60 (BOOT0)
/Microcontroller/BOOT1: J3.2, U1.28 (PB2-BOOT1_(SPI3_MOSI))
/Microcontroller/CAN_RX_IND: D2.2 (A), U1.43 (PA10)
/Microcontroller/CAN_TX_IND: D3.2 (A), U1.42 (PA9_(I2C3_SMBA_SPI2_SCK))
/Microcontroller/CS: U1.20 (PA4_(SPI1/3_NSS)); also elsewhere on the board
/Microcontroller/MISO: U1.22 (PA6_(SPI1_MISO)); also elsewhere on the board
/Microcontroller/MOSI: U1.23 (PA7_(SPI1_MOSI)); also elsewhere on the board
/Microcontroller/NRST: J4.1, U1.7 (NRST)
/Microcontroller/PC13_LED: U1.2 (PC13)
/Microcontroller/SCK: U1.21 (PA5_(SPI1_SCK)); also elsewhere on the board
/Microcontroller/SCL_(ISO): U1.58 (PB6_(I2C1_SCL)); also elsewhere on the board
/Microcontroller/SDA_(ISO): U1.59 (PB7_(I2C1_SDA)); also elsewhere on the board
/Microcontroller/SWCLK: J4.9, U1.49 (PA14_(JTCK-SWCLK))
/Microcontroller/SWDIO: J4.8, U1.46 (PA13_(JTMS-SWDIO))
/Microcontroller/UART_RX: J2.3, U1.54 (PD2)
/Microcontroller/UART_TX: J2.2, U1.53 (PC12)
/Microcontroller/VCAP_1: C11.1, C12.1, U1.30 (VCAP_1)
/Microcontroller/XTAL32_IN: C4.1, U1.3 (PC14_(OSC32_IN)), Y2.2
/Microcontroller/XTAL32_OUT: R29.2, U1.4 (PC15_(OSC32_OUT))
/Microcontroller/XTAL_IN: C1.1, R4.2, U1.5 (PH0_(OSC_IN)), Y1.1 (XTAL_IN)
/Microcontroller/XTAL_OUT: R28.1, U1.6 (PH1_(OSC_OUT))
unnamed: C2.1, R4.1, R28.2, Y1.2 (XTAL_OUT)
unnamed: C3.1, R29.1, Y2.1
unnamed: D1.1 (K), R1.2
unnamed: D2.1 (K), R2.2
unnamed: D3.1 (K), R3.2

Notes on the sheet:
I/O Required - LSD circuit for Relay - Current Sense Inputs (4 Analogue Inputs) - isoSPI
Note: Place Close to VDD Pins!
Note: Place Close to V_CAP Pin!

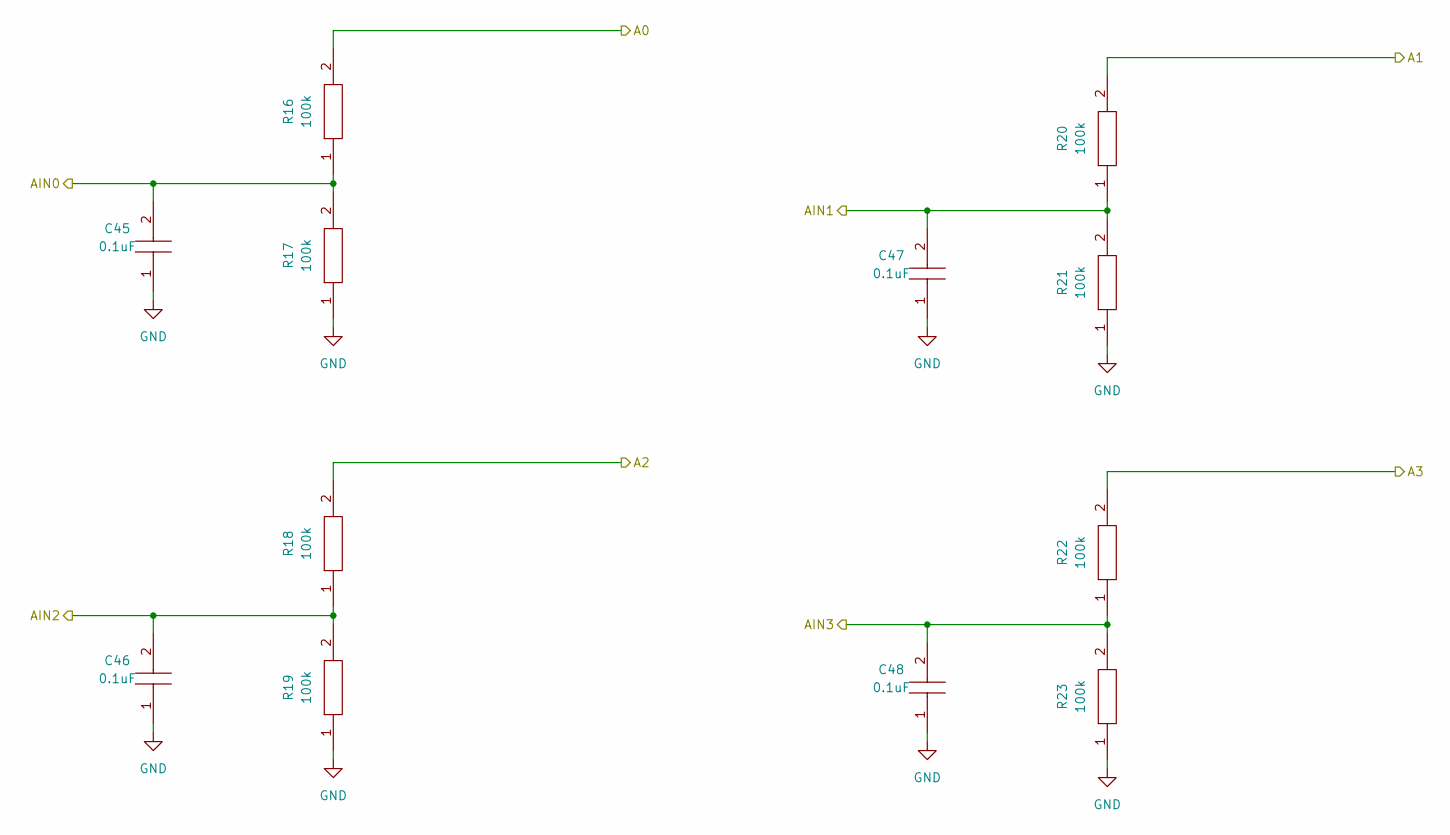
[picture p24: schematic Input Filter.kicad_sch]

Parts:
C45, C46, C47, C48: 0.1uF; C_0603_1608Metric_Pad1.08x0.95mm_HandSolder; Manufacturer_Part_Number CC0805JRX7R8BB104; Mouser Part Number 603-CC805JRX7R8BB104
R16, R17, R18, R19, R20, R21, R22, R23: 100k; R_0603_1608Metric_Pad0.98x0.95mm_HandSolder; Manufacturer_Part_Number ERJP06F1000V

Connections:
/CS1A: R16.2; also elsewhere on the board
/CS1B: R20.2; also elsewhere on the board
/CS2A: R18.2; also elsewhere on the board
/CS2B: R22.2; also elsewhere on the board
/Current Sense/Input Filter/AIN0: C45.2, R16.1, R17.2; also elsewhere on the board
/Current Sense/Input Filter/AIN1: C47.2, R20.1, R21.2; also elsewhere on the board
/Current Sense/Input Filter/AIN2: C46.2, R18.1, R19.2; also elsewhere on the board
/Current Sense/Input Filter/AIN3: C48.2, R22.1, R23.2; also elsewhere on the board
GND: C45.1, C46.1, C47.1, C48.1, R17.1, R19.1, R21.1, R23.1; also elsewhere on the board



Board: 4 copper layers, 77.5 x 46.9 mm, 111 parts (32 on the bottom side), 69 nets.

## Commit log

2023-04-17 New boards
    [230408 BSPD Current Sense Board R2.PrjPcb, Power supply.SchDoc, TopLevel.SchDoc]
2023-04-17 Aero board
    [CAN.SchDoc, Diff_Pressure_Sensors.PrjPcb, Multiplexer Bank.SchDoc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]
2023-04-20 Power supply
    [PCB1.PcbDoc, Power supply - Copy (2).SchDoc, Power_Supply.PrjPcb]
2023-04-21 Dashboard Breakout Board Started
    Schematic almost complete, just needs power supply added. Made for 4 buttons and a potentiometer. Uses 1 CAN line with Molex MicroFit connectors
    [436500500.stp, 436500600.stp, 436500700.stp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]
2023-04-21 Dashboard: First components placed
    [CAN.SchDoc, Power supply - Copy (2).SchDoc, TS_23 Dashboard Breakout Board.PrjPcb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]
2023-04-22 Dashboard Rev 1 has been completed
    Ready for internal review
    [Power supply - Copy (2).SchDoc, Top_Level.SchDoc]
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2023-05-09 LV_BMS_A Sample Uploads
    [Balancing and Filtering.kicad_sch, Blue Loop.kicad_sch, CANBUS.kicad_sch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]
2023-05-09 Fix Diff. Pair Routing on Slave
    [LVBMS_A_Sample_R2.kicad_pcb]
2023-05-10 resolved diff. pair routing issues on master module
    [LV_MASTER_A_SAMPLE.kicad_pcb]
2023-05-10 Last Minute Changes
    [LV_MASTER_A_SAMPLE-B_Cu.gbl, LV_MASTER_A_SAMPLE-B_Fab.gbr, LV_MASTER_A_SAMPLE-B_Mask.gbs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]
2023-05-10 Minor Changes
    [LV_MASTER_A_SAMPLE PCB.step.SLDPRT, LV_MASTER_A_SAMPLE.kicad_sch, MCU.kicad_sch]
2023-05-17 Started new power system
    [CAN.SchDoc, Molex Microfit Single Row.PcbLib, Molex Microfit Single Row.SchLib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]
2023-05-18 New Power Supply - Half done
    Added a new 24 to 5 V reg that is much smaller, mostly wired up, added a bunch of new capacitors that will also be added to the standard library
    [Power supply - Copy (2).SchDoc]
2023-05-19 Dashboard PCB getting there
    [CAN.SchDoc, Power supply - Copy (2).SchDoc, TS_23 Dashboard Breakout Board.PrjPcb]
2023-05-21 Temp Module Progress as at 21/05/2023
    Schematic design completed. PCB design in progress. Fundamental changes in schematic and PCB design coming soon to adhere to comp rules.
    [CAN.SchDoc, FSAES-22-E17 Temp Module.PrjPcb, Microcontroller.SchDoc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]
2023-06-03 Final Changes to board
    [Blue Loop.kicad_sch, LV_MASTER_A_SAMPLE.kicad_pcb, LV_MASTER_A_SAMPLE.kicad_sch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]
2023-06-13 Dashboard PCB R0 completed, ready for review
    [070323 Terminal Board R3.PrjPcb, Harwin Spring Contacts.PcbLib, Harwin Spring Contacts.SchLib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]
2023-06-15 R0 of Dashboard Breakout Board ready for final review before Sourceman
    Terminal Board is also close to being ready for final review
    [070323 Terminal Board R3.PrjPcb, PCB.PcbDoc, Schematic.SchDoc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]
2023-06-18 Terminal Board R3
    Terminal Board R3 ready for review before sending to Sourceman for manufacture
    [PCB.PcbDoc, Schematic.SchDoc]
2023-06-25 LV BMS Updates
    [LVBMS_A_Sample_R2.kicad_pcb, LVBMS_A_Sample_R2.kicad_sch]
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2023-07-03 Still more fab stuff
    [LVBMS_A_Sample_R2-B_Cu.gbl, LVBMS_A_Sample_R2-B_Fab.gbr, LVBMS_A_Sample_R2-B_Mask.gbs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]
2023-07-03 Completed Temp Module Design
    [CAN.SchDoc, FSAES-22-E17 Temp Module.PrjPcb, FSAES-23-E17 Temp Module.PrjPcb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]
2023-07-16 Added CAD for Temp Module Assembly
    [Temp_Module_Enclosure_Base.SLDPRT, Temp_Module_Enclosure_Lid.SLDPRT]
2023-07-16 Update to Temp Module Assembly CAD
    Changed bolt hole diameter sizes for tabs and fixed interferences.
    [Temp_Module_Enclosure_Base.SLDPRT, Temp_Module_Enclosure_Lid.SLDPRT]
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2023-07-28 New Brake Module Upload
    [BSPD.SchDoc, CAN.SchDoc, Input Filter.SchDoc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]
2023-07-28 Brake Module R6 Layout Fixes
    [BSPD.SchDoc, Microcontroller.SchDoc, Safety Loops.SchDoc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]
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2023-08-20 Rough design for PDM
    Still need to add Bridge Drivers and connect some of the comms lines to the micro
    [CAN.SchDoc, Microcontroller.SchDoc, PCB_Project.PrjPcb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]
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2023-08-27 More work on PDM
    [Digital Isolation.SchDoc, PCB_Project.PrjPcb, Power Outputs.SchDoc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]
2023-08-27 Schematic done aside from main connector
    [Digital Isolation.SchDoc, Microcontroller.SchDoc, PCB_Project.PrjPcb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]
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2023-09-03 copy of pcb is what ive done for the low voltage side
    [Digital Isolation.SchDoc, Microcontroller.SchDoc, PWM Signal Isolation.SchDoc]
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2023-09-03 Roughly placed H bridge and smart switches on PDM
    [PCB_Project.PrjPcb, Power Outputs.SchDoc, Power Supply.SchDoc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]
2023-09-04 Fixed Blade Fuse Holder in PCB
    [Digital Isolation.SchDoc, PCB_Project.PrjPcb, Power Supply.SchDoc]
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2023-09-05 Traces for PDM - Smart Switches are getting there
    [PCB_Project.PrjPcb]
2023-09-06 PDM Smart Driver Routing continued
    About half done
    [Top_Level.SchDoc]
2023-09-07 TS schematic for ESF mostly finished
    [ESF Schematics TS_23.PrjPcb, Tractive System Schematic.SchDoc]
2023-09-07 TS Schematics finished for ESF
    [Accumulator TS Circuits.SchDoc, Tractive System Schematic.SchDoc]
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2023-09-08 Upload Charger Schematic V2
    [200415 Brake Module R5.PrjPcb, Charger TopLevel.SchDoc, TS_Charger.PrjPcb]
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2023-09-10 PDM almost ready for submission
    [CAN.SchDoc, Digital Isolation.SchDoc, Microcontroller.SchDoc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]
2023-09-20 Brake Module and Charger Items
    [TS_Charger.PrjPcb]
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2023-09-25 Fixed up errors
    - DECAP config on ADC
    - Added caps between AVDD/DVDD and gnd
    [CAN.SchDoc, FSAES-23-E17 Temp Module.PrjPcb, Microcontroller.SchDoc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]
2023-09-27 Changes made to ADC to temp sensor traces.
    [Temp Bank.SchDoc, Top Level.SchDoc]
2023-09-27 Fixed grounding after re-routing traces.
    [CAN.SchDoc, Microcontroller.SchDoc, Power Supply.SchDoc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]
2023-09-28 Final touch ups before second design review.
    [CAN.SchDoc, FSAES-23-E17 Temp Module.PrjPcb, Microcontroller.SchDoc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]
2023-09-28 Temp Module changes post PCB review.
    - Added power connector labels on backside of board.
    - Changed footprint for 24 to 5V power supply.
    [Power Supply.SchDoc]
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2023-10-04 Brake Module Updates for Re-Fabrication
    [BSPD.SchDoc, CAN.SchDoc]
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
